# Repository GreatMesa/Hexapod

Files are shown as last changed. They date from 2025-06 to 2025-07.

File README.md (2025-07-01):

# Arduino Servo-Powered Hexapod

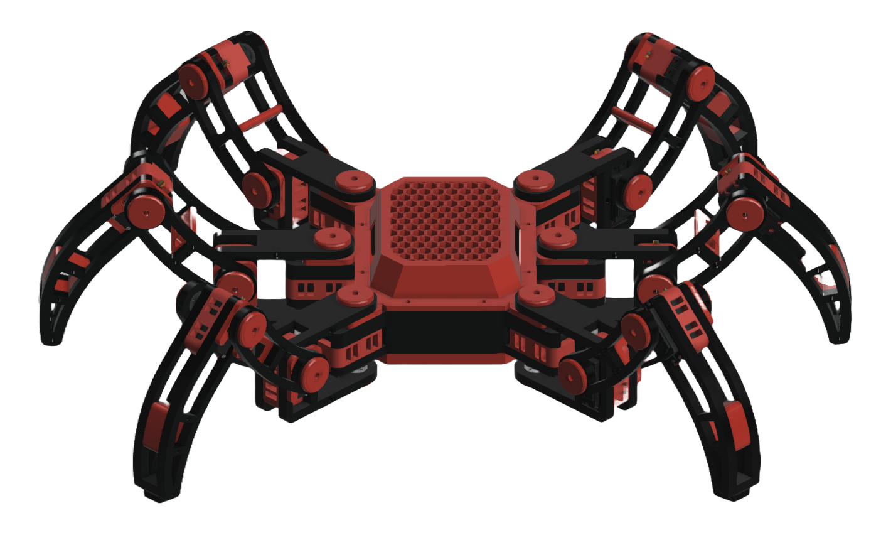
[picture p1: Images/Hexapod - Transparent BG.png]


This hexapod robot is a six-legged walking remote controlled robot that is designed for experimental and recreational purposes.

## Introduction
The 6 legs on the robot are designed to be as stable as possible, this means that the robot doesn't have to spend as much of its power in active stabilization. Besides that, the robot is also made with 3 degree of freedom, which not only model a normal leg of a anthropod but also designates a part of the leg for horizontal, vertical, and extensional movements respectfully. This gives the robot 18 degrees of freedom in total, allowing for more complex walking gait cycles and overall complex movements such as jumping, turning, and speed adjustments. With this alongside potential future sensor integration, I plan to make a robot that can effectively traverse the enviroment around it.

## Manufacturing / Parts (Mechanical Aspect)
For the mechanical aspect of this project I decided to split it into non-custom mechanical part selection, non-custom electrionics selection, custom part manufacturing, and bill of materials. This allows me to better explain each proccess instead of it being all lumped together.

### Non-Custom Mechanical Part Selection
For the servo motors, I want to use the DSServo 35KG servos due to their fast speed and high load tolerance. For the bearings (to reduce the friction on the legs) I utilized the MR148ZZ Deep Groove Ball Bearings due to how small yet efficient they were. For the screws, I selected M3 screws due to being the screw sizes that are standard for the servos I would be using while also being regularly used on 3D prints. Finally, the heated inserts I selected were the M3 3 * 4 * 5 inserts ude to interacting with the M3 screws.

### Non-Custom Electronics Selection
For the Arduino board, the only Arduino that had enough pins for what I wanted to accomplish was the Arduino Mega, although I am pondering a switch to the Arduino Mega Mini to have more space. For the wireless communication protocol I am using 2 NRF24L01+ modules. Besides these 2 sensors I also want to integrate sensors for the robot such as the MPU-6050, and for the RC Transceiver I plan to update this list with the according sensors.

### Custom Part Manufacturing
I plan to use Elegoo Plan PLUS to print out all the custom parts of the hexapod. This filament is good because it is inexpensive for how well it functions. Elegoo Pla Plus gives me the required strength I need for these parts while also allowing me to use a lower than normal infill percentage (15 %). I also plan to use 2 seperate colors (black and red) to not only distinguish between parts, but to also have a cool black spiderman color scheme.



# Component Purchase List

| Item Name | Price (USD) | Quantity | Total Price (USD) | Purchase Link |
|---|---|---|---|---|
| Dsservo 35KG DS3235 Metal Gear Digital Servo | $8.37 | 20 | $167.67 | [Alibaba](https://www.alibaba.com/product-detail/Dsservo-Waterproof-Servo-High-Torque-35KG_62204650069.html) |
| Chanzon Header Strip for Arduino GPIO 40-pin x 20pcs Female/Male Pins | $9.99 | 1 | $9.99 | [Amazon](https://www.amazon.com/gp/product/B09MY5MJ36) |
| HiLetgo 4pcs NRF24L01+ | $7.89 | 1 | $7.89 | [Amazon](https://www.amazon.com/gp/product/B00LX47OCY) |
| 1600 Pcs M3 Screw Kit, M3 Button Head and Socket Head Screws | $15.00 | 1 | $15.00 | [Amazon](https://www.amazon.com/Takytao-Button-Screws-Machine-Assortment/dp/B0D3TRRKSG) |
| SUNLU TPU 3D Printer Filament 1.75mm | $23.99 | 1 | $23.99 | [Amazon](https://www.amazon.com/SUNLU-TPU-Filament-1-75mm-Flexible/dp/B0BXNWK6NS) |
| ELEGOO PLA Plus Filament 1.75mm Red 1KG | $19.99 | 1 | $19.99 | [Amazon](https://www.amazon.com/ELEGOO-Filament-Dimensional-Accuracy-Compatible/dp/B0BM72LMQH) |
| ELEGOO PLA Plus Filament 1.75mm Black 1KG | $16.99 | 1 | $16.99 | [Amazon](https://www.amazon.com/ELEGOO-Filament-Dimensional-Accuracy-Compatible/dp/B0BM721XHT) |
| MEGA 2560 PRO Embed | $17.99 | 1 | $17.99 | [Amazon](https://www.amazon.com/Songhe-MEGA-2560-ATMEGA2560-Pro-Pinheader/dp/B07TGF9VMQ) |
| BOJACK 3 Values 130 Pcs Solderless Breadboard | $9.99 | 1 | $9.99 | [Amazon](https://www.amazon.com/BOJACK-Values-Solderless-Breadboard-Flexible/dp/B08Y59P6D1) |
| 24 Values Electrolytic Capacitor Assortment Kit | $9.99 | 1 | $9.99 | [Amazon](https://www.amazon.com/ALLECIN-Electrolytic-Capacitor-Assortment-Kit/dp/B0C1VBXCQM) |
| QTEATAK 2Pcs AC 20A/125V 15A/250V DPST 4 Pins 2 Position Switch | $7.99 | 1 | $7.99 | [Amazon](https://www.amazon.com/Position-Rocker-Toggle-Switch-QTEATAK/dp/B08614BYNC) |
| 100Pcs 6x6x5 mm Miniature Micro Momentary Tactile Tact Touch Push Button | $5.99 | 1 | $5.99 | [Amazon](https://www.amazon.com/DAOKI-Miniature-Momentary-Tactile-Quality/dp/B01CGMP9GY) |
| JFtech 5 Pairs Deans T Plug Connector with 100mm 14 AWG Wire | $9.99 | 1 | $9.99 | [Amazon](https://www.amazon.com/gp/product/B09N8WLC2B) |
| HiLetgo ILI9341 2.8" SPI TFT LCD Display Touch Panel 240X320 | $16.39 | 1 | $16.39 | [Amazon](https://www.amazon.com/HiLetgo-240X320-Resolution-Display-ILI9341/dp/B073R7BH1B) |
| HiLetgo 10pcs 4 Channels IIC I2C Logic Level Converter | $7.49 | 1 | $7.49 | [Amazon](https://www.amazon.com/HiLetgo-Channels-Converter-Bi-Directional-3-3V-5V/dp/B07F7W91LC) |

**Total Amount: $347.34**

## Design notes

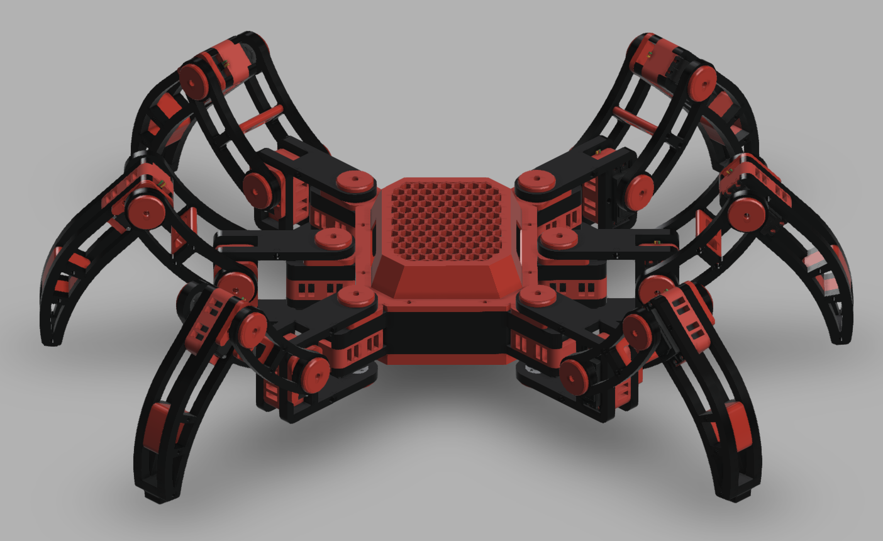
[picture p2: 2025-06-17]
Images/Hexapod.png

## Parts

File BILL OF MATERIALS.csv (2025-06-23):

Item Name | Price (USD) | Quantity | Total Price (USD) | Purchase Link
Dsservo 35KG DS3235 Metal Gear Digital Servo | $8.37 | 18 | $167.67 | (Alibaba) https://www.alibaba.com/product-detail/Dsservo-Waterproof-Servo-High-Torque-35KG_62204650069.html
Chanzon Header Strip for Arduino GPIO 40-pin x 20pcs Female/Male Pins | $9.99 | 1 | $9.99 | (Amazon) https://www.amazon.com/gp/product/B09MY5MJ36/ref=ewc_pr_img_1?smid=A14FP9XIRL6C1F&th=1
HiLetgo 4pcs NRF24L01+ | $7.89 | 1 | $7.89 | (Amazon) https://www.amazon.com/gp/product/B00LX47OCY/ref=ewc_pr_img_3?smid=A30QSGOJR8LMXA&psc=1
1600 Pcs M3 Screw Kit, M3 Button Head and Socket Head Screws | $15.00 | 1 | $15.00 | (Amazon) https://www.amazon.com/Takytao-Button-Screws-Machine-Assortment/dp/B0D3TRRKSG
SUNLU TPU 3D Printer Filament 1.75mm | $23.99 | 1 | $23.99 | (Amazon) https://www.amazon.com/SUNLU-TPU-Filament-1-75mm-Flexible/dp/B0BXNWK6NS
ELEGOO PLA Plus Filament 1.75mm Red 1KG | $19.99 | 1 | $19.99 | (Amazon) https://www.amazon.com/ELEGOO-Filament-Dimensional-Accuracy-Compatible/dp/B0BM72LMQH
ELEGOO PLA Plus Filament 1.75mm Black 1KG | $16.99 | 1 | $16.99 | (Amazon) https://www.amazon.com/ELEGOO-Filament-Dimensional-Accuracy-Compatible/dp/B0BM721XHT
MEGA 2560 PRO Embed | $17.99 | 2 | $35.98 | https://www.amazon.com/Songhe-MEGA-2560-ATMEGA2560-Pro-Pinheader/dp/B07TGF9VMQ
BOJACK 3 Values 130 Pcs Solderless Breadboard | $9.99 | 1 | $9.99 | (Amazon) https://www.amazon.com/BOJACK-Values-Solderless-Breadboard-Flexible/dp/B08Y59P6D1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
24 Values Electrolytic Capacitor Assortment Kit | $9.99 | 1 | $9.99 | (Amazon) https://www.amazon.com/ALLECIN-Electrolytic-Capacitor-Assortment-Kit/dp/B0C1VBXCQM?s=industrial
2PCS Hall Effect 3D Analog Sensor Joystick | $9.99 | 1 | $9.99 | (Amazon) https://www.amazon.com/Effect-Analog-Joystick-Replacement-Potentiometer/dp/B0CNX15ZX3?gQT=1
QTEATAK 2Pcs AC 20A/125V 15A/250V DPST 4 Pins 2 Position Switch | $7.99 | 1 | $7.99 | (Amazon) https://www.amazon.com/Position-Rocker-Toggle-Switch-QTEATAK/dp/B08614BYNC?s=industrial
100Pcs 6x6x5 mm Miniature Micro Momentary Tactile Tact Touch Push Button | 5.99 | 1 | 5.99 | https://www.amazon.com/DAOKI-Miniature-Momentary-Tactile-Quality/dp/B01CGMP9GY?s=industrial
WWZMDiB 6Pcs EC11 Rotary Encoder | 8.88 | 1 | 8.88 | https://www.amazon.com/WWZMDiB-Encoder-Digital-Potentiometer-Arduino/dp/B0C6Q67V97?s=industrial
Total Amount |  |  | $347.47

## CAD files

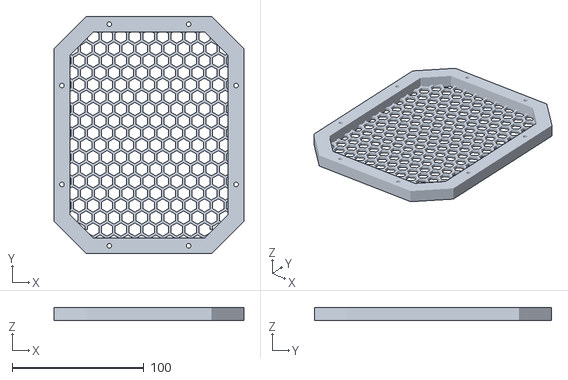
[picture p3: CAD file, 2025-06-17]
Mechanical/STL Files/Bottom Frame v5.stl
144.0 x 180.0 x 10.00

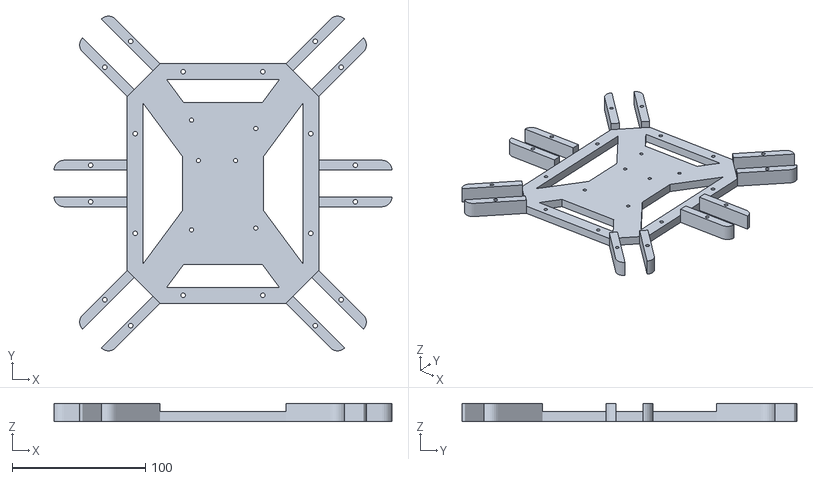
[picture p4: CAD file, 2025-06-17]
Mechanical/STL Files/Top Frame v7.stl
254.0 x 251.5 x 13.7

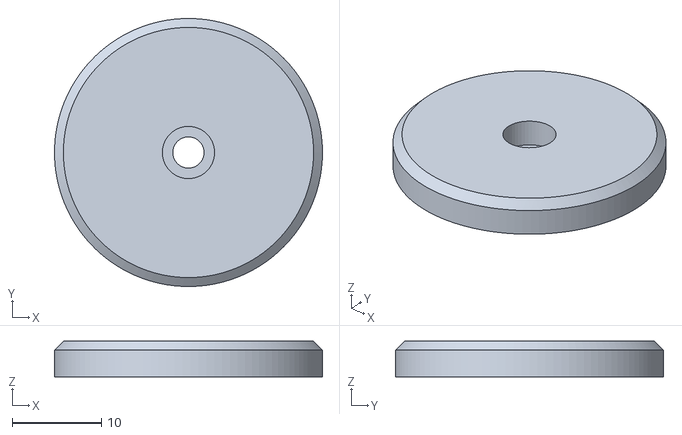
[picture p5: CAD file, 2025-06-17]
Mechanical/STL Files/crew Cap v3.stl
30.0 x 30.0 x 4.00

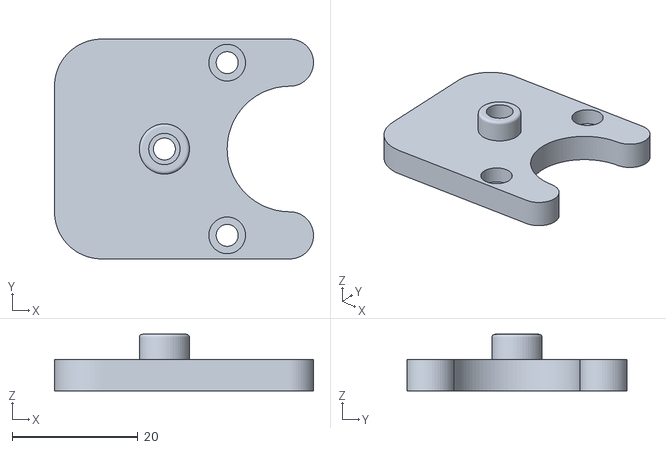
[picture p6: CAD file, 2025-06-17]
Mechanical/STL Files/Bearing Axle v7.stl
41.2 x 35.0 x 9.00

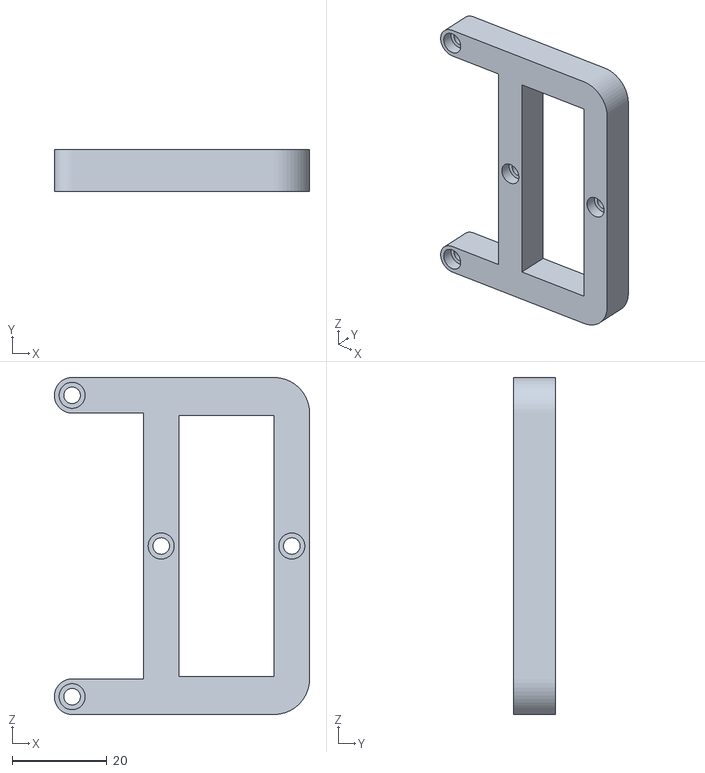
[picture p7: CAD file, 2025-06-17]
Mechanical/STL Files/Femur Horn Brace v2.stl
53.7 x 8.75 x 71.0

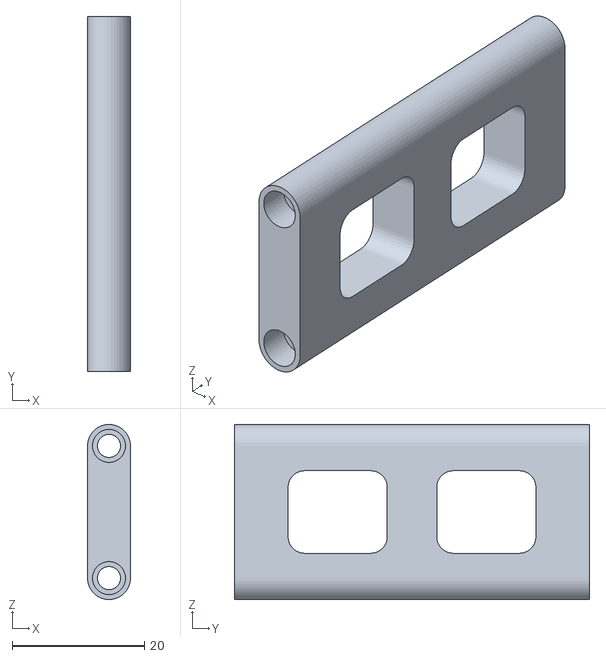
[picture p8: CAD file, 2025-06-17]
Mechanical/STL Files/Femur Brace v3.stl
6.50 x 53.8 x 26.5

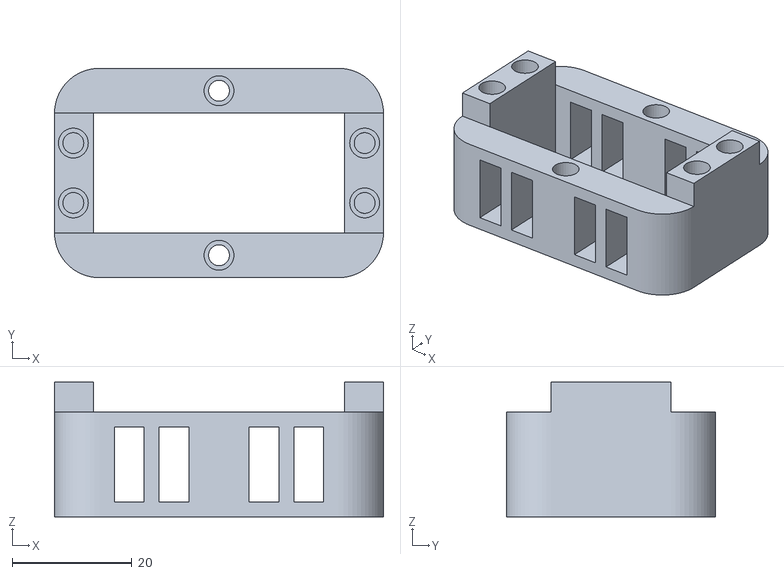
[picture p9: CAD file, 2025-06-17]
Mechanical/STL Files/Cage v2.stl
55.0 x 35.0 x 22.5

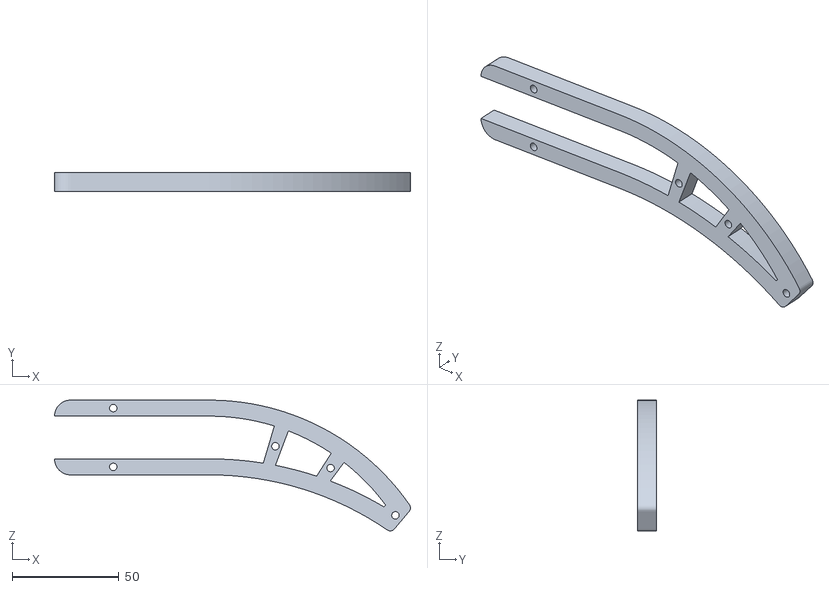
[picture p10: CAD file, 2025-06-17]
Mechanical/STL Files/Tibia Bearing Side v4.stl
166.6 x 8.75 x 61.2

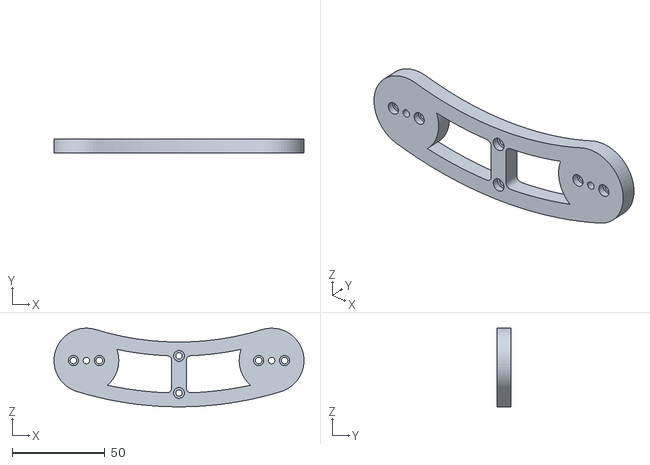
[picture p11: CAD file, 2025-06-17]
Mechanical/STL Files/Femur Horn Side v2.stl
135.0 x 7.50 x 42.5

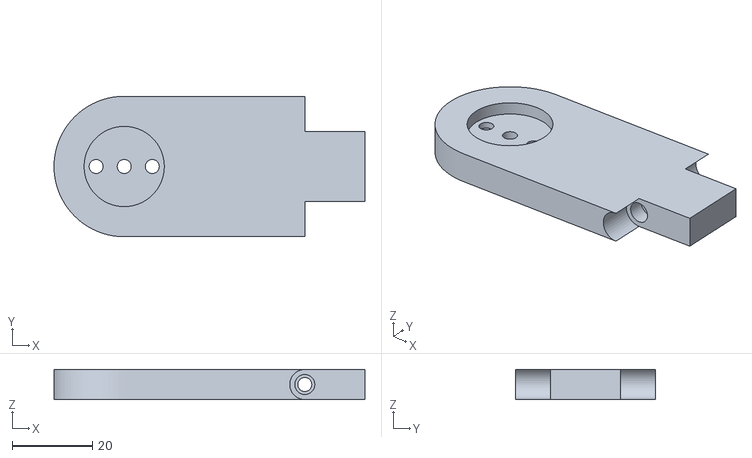
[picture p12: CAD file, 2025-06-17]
Mechanical/STL Files/Horn Coxa Side v3.stl
77.5 x 35.0 x 7.50

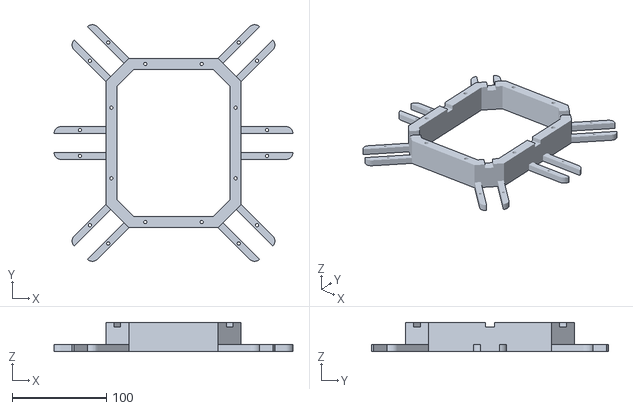
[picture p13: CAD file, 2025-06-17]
Mechanical/STL Files/Body v3.stl
254.0 x 251.5 x 31.2

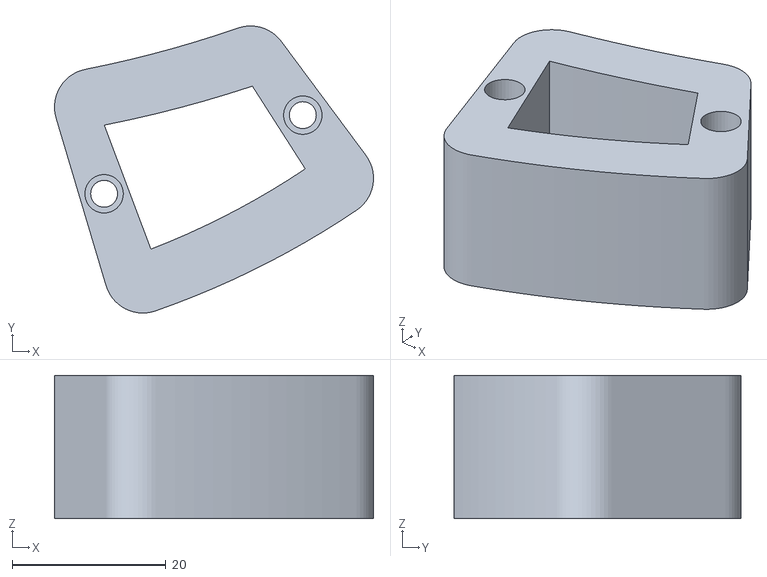
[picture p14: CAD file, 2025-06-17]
Mechanical/STL Files/Tibia Brace.stl
41.5 x 37.3 x 18.6

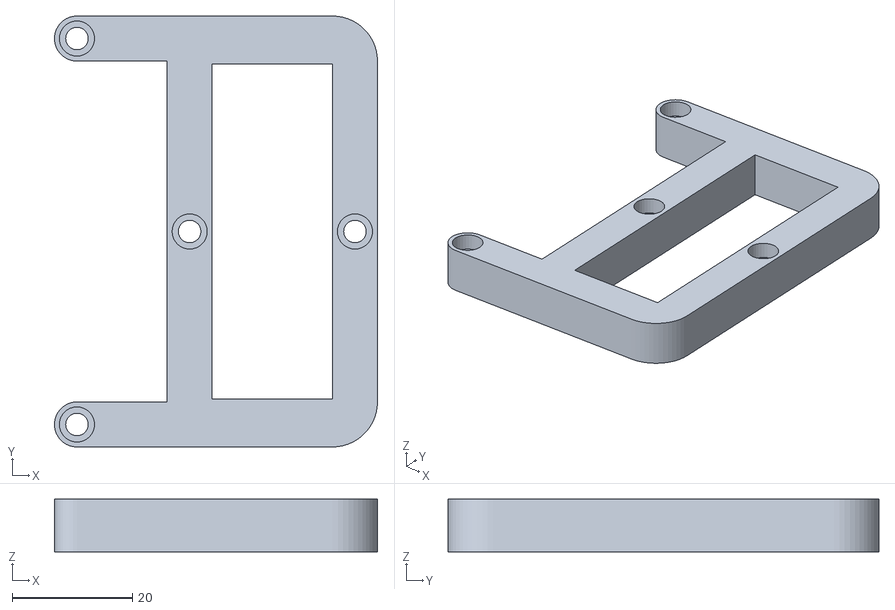
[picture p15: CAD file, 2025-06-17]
Mechanical/STL Files/Bearing Coxa Side.stl
53.7 x 71.7 x 8.75

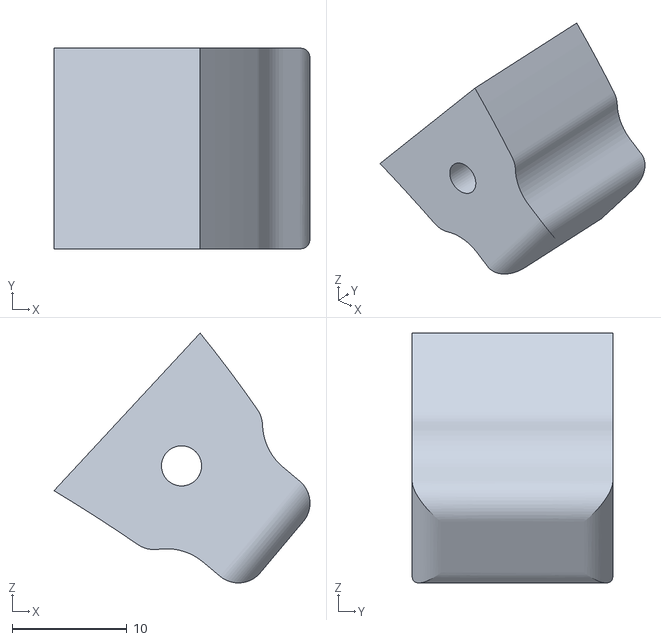
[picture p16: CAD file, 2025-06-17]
Mechanical/STL Files/Stub v2.stl
22.3 x 17.5 x 21.8

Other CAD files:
Mechanical/STL Files/Tibia Horn Side v2.stl
Mechanical/STL Files/Femur Bearing Side v2.stl
Mechanical/STL Files/Femur Bearing Brace v2.stl
Mechanical/STL Files/Bearing Coxa Side v1.stl
Mechanical/STL Files/Bearing Axle v6.stl
Mechanical/STL Files/Screw Cap.stl
Mechanical/STL Files/Top Frame v4.stl
Mechanical/STL Files/Top Frame v5.stl
Mechanical/STL Files/Top Frame v6.stl

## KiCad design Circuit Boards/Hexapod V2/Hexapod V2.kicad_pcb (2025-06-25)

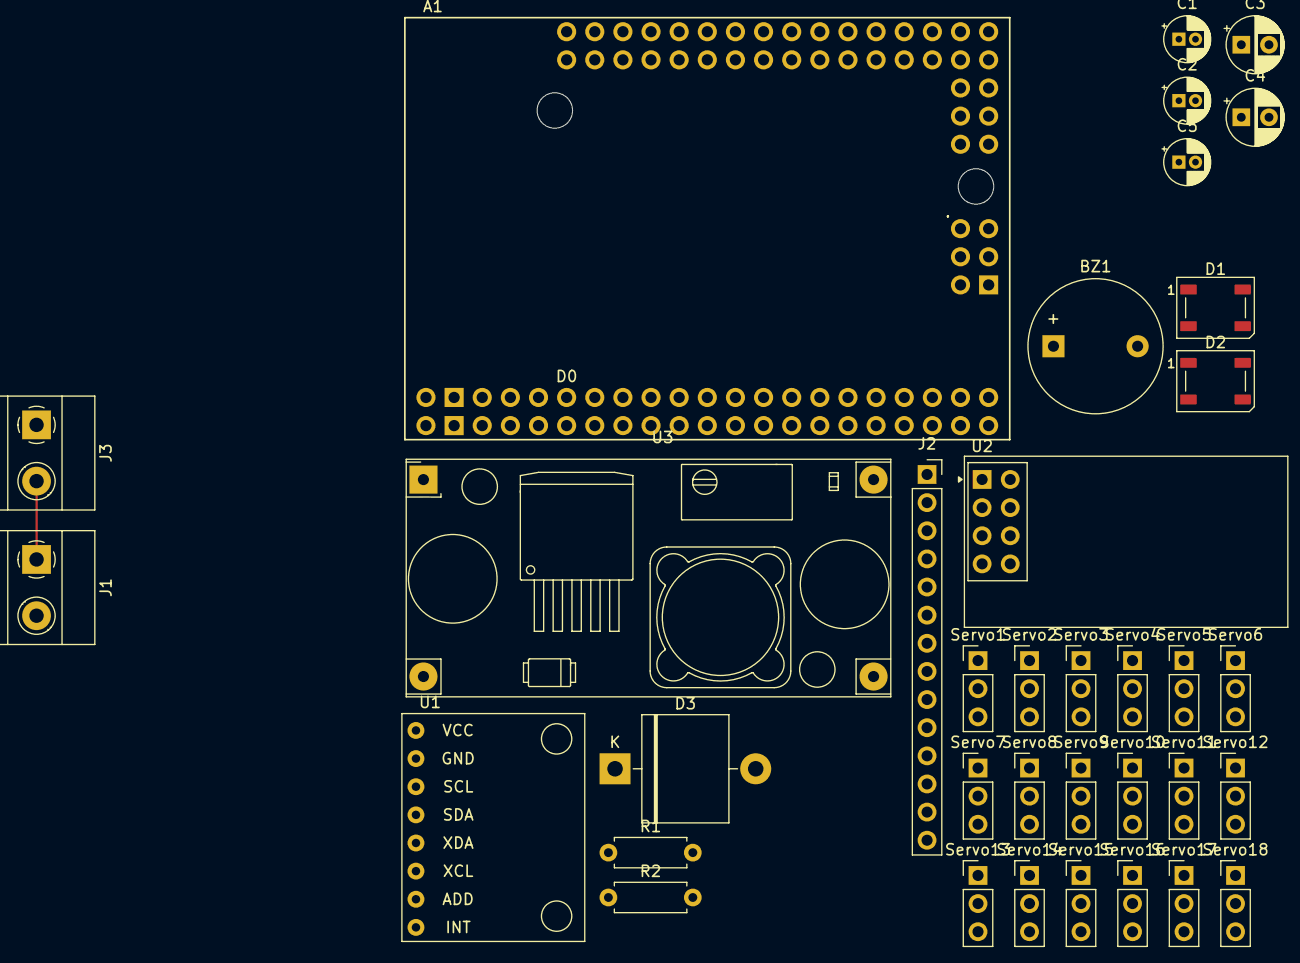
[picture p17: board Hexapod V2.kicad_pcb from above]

Board: 4 copper layers, 36 parts (0 on the bottom side), 34 nets.

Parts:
A1: Aurduino Mega 2560 Pro; Clone_Mega2560_Pro_Socket
BZ1: Buzzer; Buzzer_12x9.5RM7.6
C1, C2: 0.1μF; CP_Radial_D4.0mm_P1.50mm
C3, C4: 100μF; CP_Radial_D5.0mm_P2.50mm
C5: 22μF; CP_Radial_D4.0mm_P1.50mm
D1, D2: WS2812B; LED_WS2812B_PLCC4_5.0x5.0mm_P3.2mm
D3: D; D_5KP_P12.70mm_Horizontal
J1: Battery; TerminalBlock_Phoenix_MKDS-1,5-2-5.08_1x02_P5.08mm_Horizont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
J2: Conn_01x14_Pin; PinSocket_1x14_P2.54mm_Vertical
J3: Switch; TerminalBlock_Phoenix_MKDS-1,5-2-5.08_1x02_P5.08mm_Horizont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
R1: 10kΩ; R_Axial_DIN0207_L6.3mm_D2.5mm_P7.62mm_Horizontal
R2: 20kΩ; R_Axial_DIN0207_L6.3mm_D2.5mm_P7.62mm_Horizontal
Servo1, Servo2, Servo3, Servo4, Servo5, Servo6, Servo7, Servo8, Servo9, Servo10, Servo11, Servo12, Servo13, Servo14, Servo15, Servo16, Servo17, Servo18: Conn_01x03_Pin; PinHeader_1x03_P2.54mm_Vertical
U1: MPU6050; module_mpu6050
U2: NRF24L01_Breakout; nRF24L01_Breakout
U3: Buck Converter; YAAJ_DCDC_StepDown_LM2596

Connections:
+3.3V: A1.3V31 (3.3V), A1.3V32 (3.3V), U1.1 (VCC)
+5V: A1.5V1 (5V), A1.5V3 (5V), C1.1, C2.1, D1.1 (VDD), D2.1 (VDD), J2.1
A1: R1.1, R2.1
A2: A1.A2, BZ1.1 (+)
CSN: A1.D53 (D53_CS), U2.4 (~CSN)
GND: A1.GND1 (GND), A1.GND2 (GND), BZ1.2 (-), C1.2, C2.2, C3.2, C4.2, C5.2, D1.3 (VSS), D2.3 (VSS), D3.2 (A), J2.2, R1.2, Servo1.1, Servo2.1, Servo3.1, Servo4.1, Servo5.1, Servo6.1, Servo7.1, Servo8.1, Servo9.1, Servo10.1, Servo11.1, Servo12.1, Servo13.1, Servo14.1, Servo15.1, Servo16.1, Servo17.1, Servo18.1, U1.2 (GND), U2.1 (GND), U3.1 (Vin)
MISO: A1.D50 (D50_MISO), J2.6, J2.12, U2.7 (MISO)
MOSI: A1.D51 (D51_MOSI), J2.9, J2.13, U2.6 (MOSI)
unnamed: J1.1, J3.2
unnamed: J1.2, U3.3 (GND)
unnamed: J3.1, U3.4 (Vout)
unnamed: C5.1, U2.2 (VCC)
S1: A1.D7, Servo1.3
S2: A1.D9, Servo2.3
S3: A1.D11, Servo3.3
S4: A1.D13, Servo4.3
S5: A1.D23, Servo5.3
S6: A1.D25, Servo6.3
S7: A1.D27, Servo7.3
S8: A1.D29, Servo8.3
S9: A1.D31, Servo9.3
S10: A1.D33, Servo10.3
S11: A1.D35, Servo11.3
S12: A1.D37, Servo12.3
S13: A1.D39, Servo13.3
S14: A1.D41, Servo14.3
S15: A1.D43, Servo15.3
S16: A1.D45, Servo16.3
S17: A1.D47, Servo17.3
S18: A1.D49, Servo18.3
SCK: A1.D52 (D52_SCK), J2.7, J2.10, U2.5 (SCK)
SCL: A1.D21 (D21/SCL), U1.3 (SCL)
SDA: A1.D20 (D20/SDA), U1.4 (SDA)
VIN: A1.VIN1 (VIN), A1.VIN2 (VIN), C3.1, C4.1, D3.1 (K), R2.2, Servo1.2, Servo2.2, Servo3.2, Servo4.2, Servo5.2, Servo6.2, Servo7.2, Servo8.2, Servo9.2, Servo10.2, Servo11.2, Servo12.2, Servo13.2, Servo14.2, Servo15.2, Servo16.2, Servo17.2, Servo18.2, U3.2 (GND)

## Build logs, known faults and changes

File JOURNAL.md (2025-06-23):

---
title: "Arduino Servo-Powered Hexapod"
author: "Chinedu Okpala"
description: "6-Legged RC-Controlled Robot"
created_at: "2025-3-01"
---
# Arduino Hexapod Journal
Total Hours Logged: 78 hrs

## Initial Reaserch 3/01/25 - 3/04/25 (5 Hours)

So when I initially started this project, I looked into different types of robots to do. I ended up deciding on the hexapod because it looked extremely cool. So during this time I looked into different type of hexapods such as commercial hexapods and hexapods that were custom built. In the end I had a list of things that I wanted to do in this project:

- Fully design the robot in Fusion 360.
- Design a custom PCB that would be used in the project.
- Develop a radio transmitter that allows me to remote control the hexapod.
- Develop inverse kinematic formulas to create walking gaits.

## Frame Construction 3/5/25 - 3/17/25 (16 Hours)

The first thing that I needed to do when designing the hexapod was the frame. As much as I didn't like it, starting off with the frame and the leg would give me a good idea on how big I wanted the hexapod to be, it would also give me an idea of how I was going to attach the servos to the robot. I decided to split up the frame of the hexapod into 4 seperate parts: the hexapod cover, the top frame, the body, and the bottom frame. I also made the servo attachment that I will be using to attach the actual servo to these projects. Throughout the next few paragraphs I will go much more into detail about each part that I constructed. However, I would construct the top cover at a later time so it will be in a later segment.

### Servo Cage 3/5/25 (2 Hours)

So the first thing that I modeled was the servo attachment that I would use to basically glue the servo to the other parts of the hexapod. I decided to name it a servo cage due to it being trapped, and effectionaly attached what looks like cage bars on the attachment for asthetic reasons.


> Servo Cage without the servo motor.


> Servo Cage with the servo motor.

The holes that are present in the cage are where the M3 heated inserts will be placed. Then where the elevated segments are placed, the servos will take place. This elevation will ironically increase the amount of space due to the elevated pieces pushing the overall body down. Also, only some segments will need heated inserts on the cage and it will entirely depend on the orientation of the servos.

### Bearing Axle 3/6/25 (1 Hour)
The bearing axle wa also a preliminary thing to do as I wanted to reduce the amount of friction on the robot. Not really much to explain about this one since it was very simple os here besides me paramterizing it for the mr148zz servo and filleting some areas for higher durability / less space. This was the bearing axle:



### Body 3/7/25 - 3/10/25 (6 Hours)

For the body, I needed to make sure that certian values were parameterized. Later on when I am programming the inverse kinematic, I will need to make sure that these values are exact, otherwise I'm fried. I decided to make a irreugular octogonal shape for the hexapod. While this may seem very odd, there is a good reason for this. With a normal hexagon, there isn't really a way to only edit one dimension due to it being a regular polygon. After this deducment I decided to work on the actual sketch. I decided to make the height longer than the width due to more room for the legs to extend. This is the sketch that I created:



As you can see, its very messy, but the parameters were there, and thats what I'm happy about. Next I needed to figure out how I would extrude it to make space for the cage. This is when I decided that the body should contain both the inner shell and the actual bottom frame. This would allow me to print it all in one chunk: increasing the stability and reducing the amount of heated inserts I need. This was the first version of the body that I would design:



However I had a problem, I realized if I were to put the top frame on the hexapod, it would be very difficult to insert the wires inside the body. I decided to make little rectangular pockets that the wires could be put. Overall, this process was very simple, and here is the second and currently final version of the hexapod's body:



Final thing about the body, I ended up putting the servo cages with the horn near the body. THis was due to the wires being oriented in the same direction, making it easier to input the wires in the body. This was the body with said servo cages:



### Top Frame 3/11/25 (2 Hours)

For the next part of the frame, I decided to start working on the top fraame, or the main attachment to the body. Since I already had an Arduino Mega at the time, I knew that I wanted to make a little indent for it. Besides that, this would be a very simple task as all I needed to do was to basically make a little sandwich with the previous . However the indent turned out to be the hardest part as I had trouble finding the arduino model. I might just be dumb but how hard it is to find a model of a arduino mega, it also doesn't help that the arduino webside doesnt have it. Either way after this was done it was simple from here, this was the arduino model I ended up with:



### Bottom Frame 3/12/25 (1 Hour)

This was by far the most simple parts of the frame construction. Later on in assembely I knew I wanted a way to suspend the hexapod in air so it would be easy to work with. The way I decided was to use a stand that I would model later, plus a bottom that could easily attach to said stand. THe bulk of the time was spent reaserching how to make a honeycomb patter. This was the final model of the body frame:



### Top Cover 3/13/25 - 3/14/25 (4 Hours)

This was the final piece for the frame, and this is personally my favorite. The goal of this part was to nicely attach to the top frame while also being a kind of shell for the arduino. Also I wanted to be able to be able to put all the servo wires neatly. I decided to make a outer layer with the same octogonal dimensions of the frame. After this I had trouble designing the slanted part due to it basically being two plates that had different y axises and were connected by slants. After some digging I realized I needed to make a inner layer to be able to loft the outer and inner plates. After that it was simple from there. I thought I would have trouble making cutouts of the slanted pieces but I realized that it worked like any normal face. Also I added a honycomb pattern to the top part since it looks cool and I could eventually attach something to it. This is a picture of the final model:



## Leg Construction 3/15/25 - 3/26/25 (29 Hours)

### Leg Design Reaserch 3/15/25 - 3/16/25 (6 Hours)

For the leg, there is a lot more complexities. Something that is important is defining the total length of the legs alongside the 3 components of the legs. The 3 segments of the leg are the Coxa, Femur, and Tibia. Someting that I learnt was that each part of the leg is directly responsible for something:

- The **Coxa** is responsible for any horizontal movement of the leg.
- The **Femur** is responsible for any vertical movements of the robot.
- The **Tibia** is responsible for any extensional / z axis movements of the robot.

Something important to mention is that depending on each task, the lengths of the robot should match that. That means the Coxa should be the smallest out of the 3 segments due to the horizontal limit actually being more affected by the Tibia, meaning that segment should be the longest.  The femur is somewhere in the middle as you want to have a good vertical range without loosing the mobility of a small tibia. 

### Coxa Construction 3/17/25 - 3/18/25 (6 Hours)

Starting off with the Coxa construction, I needed to both extend the brace outside the frame, but to also house the femur servo. The first part I would start with was the extension part. It was fairly simple as all I needed to do was to make sure the end of it was outside the frame. The brace was also fairly simple, all I needed to do was to make sure it fitted the cage insdie of it. This was the model I came up with:



Also I added hubcaps so that I could tune the friction since I saw people having problems with overcorrection with the PID loop of the servo.

### Femur Construction 3/19/25 - 3/20/25 (7 Hours)

Now onto the Femur. Something important that I needed to do was to make the leg curved. I realized that if I wanted to save space on the robot, a curved Femur would allow me to bend the legs much more into the frame than normal. For the length of the Femur I decided to make it 100 cm due to it being a nice number and it also was a good length compared to what I wanted the tibia to be. Also I figured out how to make the curved Femur by making a curved tangent spline. One final thing is that I made indents for the horn side and bearing side, while making a small brace to connect the sides. Here is the femur model.



### Tibia Construction 3/21/25 - 3/25/25 (10 Hours)

This took by far, by far, the most amount of time and was easily the most annoying part of the leg. The problem arrises when I wanted to make the leg curved. Unlike the femur sketch, there is a actual angle between the beginning and end point of the tibia. There are a multitude of reasons why a curved leg is better, with shock absorbtion and higher stability topping the list. However actually making the curved leg with a angle that needs to be known for the inverse kinematics was quite diabolical. Turns out I basically needed to make multiple circles to draw out each part of the tibia, something that took me a long time to realize. However, after this it was fairly simple from there as both the complex geometry of the stub and the tibia brace were fairly straight foward. Here is the sketch of and the acutal tibia:


>Sketch


>Actual Tibia

## Assembely 3/26/25 (4 Hours)

So, turns out when I was origionally doing this (since cadding was a new experience), I had everything in one janky file. I realized in order to get a better model of this hexapod and attach all the legs I needed to split every component up and then put them back together. Needless to say but this took a good amount of time to put together, but it looks absolutely amazing and I am super proud of this model. This is the final model in fusion 360:

Hexapod

## Hexapod PCB Design V1 (25 Hours)

### Initial Reaserch 3/30/25 - 3/31/25 (4 Hours)
For the PCB of the hexapod, I originally wanted to make a shield for an Arduino Mega. This would allow me to just shlap it on the arduino mega and somewhat be done with it. After doing some reaserch, the only electronics I wanted was the communication NRF, and a stable power supply. However in the future I want to make the PCB an actual pcb. But lets see how that goes.

### Schematic Design 4/7/25 - 4/11/25 (9 Hours)

Throughout this week I decided to start and finish the schematic. This was also my first time doing schematics so it took time learning KiCad in general. Once I got a hang of it, I was chilling. Here is a picture o the schematic that I came up with and I will just write some more notes about spesific things:



- The reason for all the pins is that there isn't a shield pin modelfor the arduino so I sliced it into bits.
- The NRF2401 needs a capacitor for a stable power supply.
- The power supply also has 2 capacitors for a overall more stable power supply.
- The GPIO blocks were going to be used for stuff like other servos and LEDs.

### PCB Routing (12 Hours)

As this was my first time routing, this was a humbling experience to say the least. Due to me at the time wanting a lot of general purpose blocks and me originally using 1 layer (pretty dumb ik ik), it took a bit to get it right. But as soon as all the difficult cases were done it was good from there, especially as soon as I knew what I was doing. This was the final routing of the shield:



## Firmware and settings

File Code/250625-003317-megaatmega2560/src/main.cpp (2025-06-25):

/*
   Arduino and MPU6050 Accelerometer and Gyroscope Sensor Tutorial
   by Dejan, https://howtomechatronics.com
*/
#include <Arduino.h>
#include <Wire.h>
const int MPU = 0x68; // MPU6050 I2C address
float AccX, AccY, AccZ;
float GyroX, GyroY, GyroZ;
float accAngleX, accAngleY, gyroAngleX, gyroAngleY, gyroAngleZ;
float roll, pitch, yaw;
float AccErrorX, AccErrorY, GyroErrorX, GyroErrorY, GyroErrorZ;
float elapsedTime, currentTime, previousTime;
int c = 0;
void setup() {
  Serial.begin(19200);
  Wire.begin();                      // Initialize comunication
  Wire.beginTransmission(MPU);       // Start communication with MPU6050 // MPU=0x68
  Wire.write(0x6B);                  // Talk to the register 6B
  Wire.write(0x00);                  // Make reset - place a 0 into the 6B register
  Wire.endTransmission(true);        //end the transmission
  /*
  // Configure Accelerometer Sensitivity - Full Scale Range (default +/- 2g)
  Wire.beginTransmission(MPU);
  Wire.write(0x1C);                  //Talk to the ACCEL_CONFIG register (1C hex)
  Wire.write(0x10);                  //Set the register bits as 00010000 (+/- 8g full scale range)
  Wire.endTransmission(true);
  // Configure Gyro Sensitivity - Full Scale Range (default +/- 250deg/s)
  Wire.beginTransmission(MPU);
  Wire.write(0x1B);                   // Talk to the GYRO_CONFIG register (1B hex)
  Wire.write(0x10);                   // Set the register bits as 00010000 (1000deg/s full scale)
  Wire.endTransmission(true);
  delay(20);
  */
  // Call this function if you need to get the IMU error values for your module
  calculate_IMU_error();
  delay(20);
}
void loop() {
  // === Read acceleromter data === //
  Wire.beginTransmission(MPU);
  Wire.write(0x3B); // Start with register 0x3B (ACCEL_XOUT_H)
  Wire.endTransmission(false);
  Wire.requestFrom(MPU, 6, true); // Read 6 registers total, each axis value is stored in 2 registers
  //For a range of +-2g, we need to divide the raw values by 16384, according to the datasheet
  AccX = (Wire.read() << 8 | Wire.read()) / 16384.0; // X-axis value
  AccY = (Wire.read() << 8 | Wire.read()) / 16384.0; // Y-axis value
  AccZ = (Wire.read() << 8 | Wire.read()) / 16384.0; // Z-axis value
  // Calculating Roll and Pitch from the accelerometer data
  accAngleX = (atan(AccY / sqrt(pow(AccX, 2) + pow(AccZ, 2))) * 180 / PI) - 0.58; // AccErrorX ~(0.58) See the calculate_IMU_error()custom function for more details
  accAngleY = (atan(-1 * AccX / sqrt(pow(AccY, 2) + pow(AccZ, 2))) * 180 / PI) + 1.58; // AccErrorY ~(-1.58)
  // === Read gyroscope data === //
  previousTime = currentTime;        // Previous time is stored before the actual time read
  currentTime = millis();            // Current time actual time read
  elapsedTime = (currentTime - previousTime) / 1000; // Divide by 1000 to get seconds
  Wire.beginTransmission(MPU);
  Wire.write(0x43); // Gyro data first register address 0x43
  Wire.endTransmission(false);
  Wire.requestFrom(MPU, 6, true); // Read 4 registers total, each axis value is stored in 2 registers
  GyroX = (Wire.read() << 8 | Wire.read()) / 131.0; // For a 250deg/s range we have to divide first the raw value by 131.0, according to the datasheet
  GyroY = (Wire.read() << 8 | Wire.read()) / 131.0;
  GyroZ = (Wire.read() << 8 | Wire.read()) / 131.0;
  // Correct the outputs with the calculated error values
  GyroX = GyroX + 0.56; // GyroErrorX ~(-0.56)
  GyroY = GyroY - 2; // GyroErrorY ~(2)
  GyroZ = GyroZ + 0.79; // GyroErrorZ ~ (-0.8)
  // Currently the raw values are in degrees per seconds, deg/s, so we need to multiply by sendonds (s) to get the angle in degrees
  gyroAngleX = gyroAngleX + GyroX * elapsedTime; // deg/s * s = deg
  gyroAngleY = gyroAngleY + GyroY * elapsedTime;
  yaw =  yaw + GyroZ * elapsedTime;
  // Complementary filter - combine acceleromter and gyro angle values
  roll = 0.96 * gyroAngleX + 0.04 * accAngleX;
  pitch = 0.96 * gyroAngleY + 0.04 * accAngleY;
  
  // Print the values on the serial monitor
  Serial.print(roll);
  Serial.print("/");
  Serial.print(pitch);
  Serial.print("/");
  Serial.println(yaw);
}
void calculate_IMU_error() {
  // We can call this funtion in the setup section to calculate the accelerometer and gyro data error. From here we will get the error values used in the above equations printed on the Serial Monitor.
  // Note that we should place the IMU flat in order to get the proper values, so that we then can the correct values
  // Read accelerometer values 200 times
  while (c < 200) {
    Wire.beginTransmission(MPU);
    Wire.write(0x3B);
    Wire.endTransmission(false);
    Wire.requestFrom(MPU, 6, true);
    AccX = (Wire.read() << 8 | Wire.read()) / 16384.0 ;
    AccY = (Wire.read() << 8 | Wire.read()) / 16384.0 ;
    AccZ = (Wire.read() << 8 | Wire.read()) / 16384.0 ;
    // Sum all readings
    AccErrorX = AccErrorX + ((atan((AccY) / sqrt(pow((AccX), 2) + pow((AccZ), 2))) * 180 / PI));
    AccErrorY = AccErrorY + ((atan(-1 * (AccX) / sqrt(pow((AccY), 2) + pow((AccZ), 2))) * 180 / PI));
    c++;
  }
  //Divide the sum by 200 to get the error value
  AccErrorX = AccErrorX / 200;
  AccErrorY = AccErrorY / 200;
  c = 0;
  // Read gyro values 200 times
  while (c < 200) {
    Wire.beginTransmission(MPU);
    Wire.write(0x43);
    Wire.endTransmission(false);
    Wire.requestFrom(MPU, 6, true);
    GyroX = Wire.read() << 8 | Wire.read();
    GyroY = Wire.read() << 8 | Wire.read();
    GyroZ = Wire.read() << 8 | Wire.read();
    // Sum all readings
    GyroErrorX = GyroErrorX + (GyroX / 131.0);
    GyroErrorY = GyroErrorY + (GyroY / 131.0);
    GyroErrorZ = GyroErrorZ + (GyroZ / 131.0);
    c++;
  }
  //Divide the sum by 200 to get the error value
  GyroErrorX = GyroErrorX / 200;
  GyroErrorY = GyroErrorY / 200;
  GyroErrorZ = GyroErrorZ / 200;
  // Print the error values on the Serial Monitor
  Serial.print("AccErrorX: ");
  Serial.println(AccErrorX);
  Serial.print("AccErrorY: ");
  Serial.println(AccErrorY);
  Serial.print("GyroErrorX: ");
  Serial.println(GyroErrorX);
  Serial.print("GyroErrorY: ");
  Serial.println(GyroErrorY);
  Serial.print("GyroErrorZ: ");
  Serial.println(GyroErrorZ);
}

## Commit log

2025-06-17 WIP: Save progress before rebase
    [Bearing Axle v6.stl, Bearing Axle v7.stl, Bearing Coxa Side v1.3mf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]
2025-06-19 Started Journal + Hexapod V2 PCB
    [BILL OF MATERIALS - Sheet1.csv, Bearing Coxa Side v1.3mf, Bearing Coxa Side.stl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]
2025-06-20 Updated Bill of Materials
    [BILL OF MATERIALS.csv]
2025-06-21 Update BILL OF MATERIALS - Sheet1.csv
    [BILL OF MATERIALS - Sheet1.csv]
2025-06-23 added new stuff
    [BILL OF MATERIALS - Sheet1.csv, BILL OF MATERIALS.csv, Hexapod V2.kicad_pcb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]
2025-06-25 Started Firmware + Continued PCB
    [Hexapod V2.kicad_pcb, Hexapod V2.kicad_sch]
